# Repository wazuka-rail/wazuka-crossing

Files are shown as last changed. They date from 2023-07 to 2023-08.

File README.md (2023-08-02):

# Wazuka-Crossing
Miniature of a Japanese-style level crossing

## Full Version (with level crossing barriers)

**Under Development**

## Simple Version (without level crossing barriers)
Level Crossing Warning Sound Generator (https://www.youtube.com/watch?v=Fo-AsSxr2Go)

### Schematic
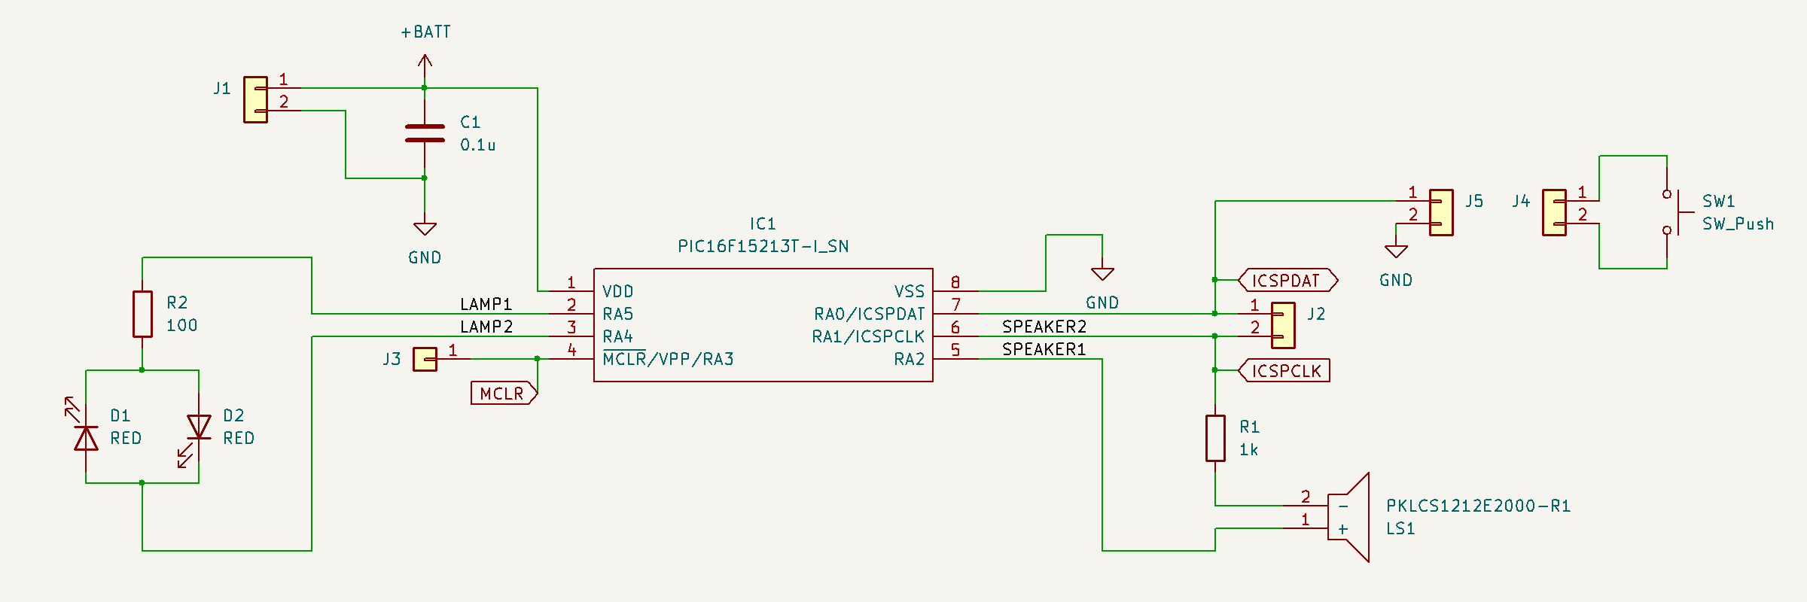
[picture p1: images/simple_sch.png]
Schematic of the simple version


### MCU
- PIC16F15213 PDIP / SOIC / DFN

|Pin| Name | Function | Target |
|---|---|---|---|
| 1 | VDD | VDD | |
| 2 | RA5 | DO | Lamp 1 |
| 3 | RA4 | DO | Lamp 2 |
| 4 | MCLR | MCLR | |
| 5 | PWM3 | PWM | Speaker 1 |
| 6 | ICSPCLK/PWM4 | ICSP/PWM | Speaker 2 |
| 7 | ICSPDAT | ICSP/DI  | Button |
| 8 | VSS | VSS | |

## Timers
| Freq.  | Timer | Purpose |
|---:|:---|---|
| 20 kHz | Timer2 | Sound PWM (PWM3) |
| 156 Hz | Timer2 / 128 | Lamp PFM (S/W) |
| ~30 Hz | Timer2 / 4 / ~150 | Sound Modulation |
| 20 Hz  | Timer0 | Train Detection, Button |
| 1.7 Hz | Timer0 / 12 | Lamp Flicker |

## Notes
The PICkit3 does not officially support the PIC16F152 family.
You can program PIC16F152 devices by PICkit3 with
[PICkitminus](http://kair.us/projects/pickitminus/).

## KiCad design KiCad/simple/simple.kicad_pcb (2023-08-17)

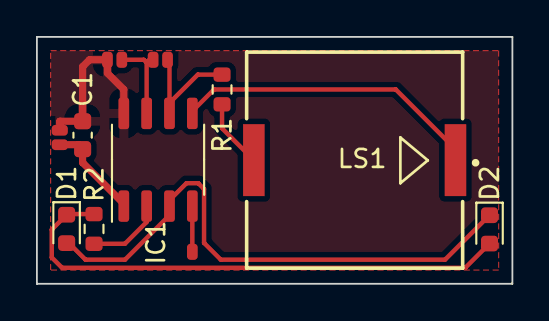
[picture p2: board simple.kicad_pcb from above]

Board: 2 copper layers, 26.4 x 13.7 mm, 11 parts (0 on the bottom side), 10 nets.

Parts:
C1: 0.1u; C_0603_1608Metric
D1, D2: RED; LED_0603_1608Metric
IC1: PIC16F15213T-I_SN; SO-8_3.9x4.9mm_P1.27mm
J1, J2, J5: Conn_01x02; JP_2T
J3: Conn_01x01; JP_1T
LS1: PKLCS1212E2000-R1
R1: 1k; R_0603_1608Metric
R2: 100; R_0603_1608Metric

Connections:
+BATT: C1.1, IC1.1 (VDD), J1.1
/LAMP1: IC1.2 (RA5), R2.1
/LAMP2: D1.2 (A), D2.1 (K), IC1.3 (RA4)
/SPEAKER1: IC1.5 (RA2), LS1.1 (+)
GND: C1.2, IC1.8 (VSS), J1.2, J5.2
ICSPCLK: IC1.6 (RA1/ICSPCLK), J2.2, R1.2
ICSPDAT: IC1.7 (RA0/ICSPDAT), J2.1, J5.1
MCLR: IC1.4 (~MCLR/VPP/RA3), J3.1
unnamed: D1.1 (K), D2.2 (A), R2.2
unnamed: LS1.2 (-), R1.1

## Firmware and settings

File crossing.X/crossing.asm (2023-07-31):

#ifdef  SIMPLE
    PROCESSOR 16F15213
#else
    PROCESSOR 16F15223
#endif

#include <xc.inc>

#include "macros.inc"

; CONFIG1
  CONFIG  FEXTOSC = OFF         ; External Oscillator Mode Selection bits (Oscillator not enabled)
  CONFIG  RSTOSC = HFINTOSC_32MHZ; Power-up Default Value for COSC bits (HFINTOSC (32 MHz))
  CONFIG  CLKOUTEN = OFF        ; Clock Out Enable bit (CLKOUT function is disabled; I/O function on RA4)
  CONFIG  VDDAR = LO            ; VDD Range Analog Calibration Selection bit (Internal analog systems are calibrated for operation between VDD = 1.8V - 3.6V)

; CONFIG2
  CONFIG  MCLRE = INTMCLR       ; Master Clear Enable bit (If LVP = 0, MCLR pin is port defined function; If LVP = 1, RA3 pin function is MCLR)
  CONFIG  PWRTS = PWRT_1        ; Power-up Timer Selection bits (PWRT set at 1 ms)
  CONFIG  WDTE = NSLEEP         ; WDT Operating Mode bits (WDT enabled while Sleep = 0, suspended when Sleep = 1; SEN is ignored)
  CONFIG  BOREN = NSLEEP        ; Brown-out Reset Enable bits (Brown-out Reset enabled while running, disabled in Sleep; SBOREN is ignored)
  CONFIG  BORV = LO             ; Brown-out Reset Voltage Selection bit (Brown-out Reset Voltage (VBOR) set to 1.9V)
  CONFIG  PPS1WAY = ON          ; PPSLOCKED One-Way Set Enable bit (The PPSLOCKED bit can be set once after an unlocking sequence is executed; once PPSLOCKED is set, all future changes to PPS registers are prevented)
  CONFIG  STVREN = ON           ; Stack Overflow/Underflow Reset Enable bit (Stack Overflow or Underflow will cause a reset)

; CONFIG3

; CONFIG4
  CONFIG  BBSIZE = BB512        ; Boot Block Size Selection bits (512 words boot block size)
  CONFIG  BBEN = OFF            ; Boot Block Enable bit (Boot Block is disabled)
  CONFIG  SAFEN = OFF           ; SAF Enable bit (SAF is disabled)
  CONFIG  WRTAPP = OFF          ; Application Block Write Protection bit (Application Block is not write-protected)
  CONFIG  WRTB = OFF            ; Boot Block Write Protection bit (Boot Block is not write-protected)
  CONFIG  WRTC = OFF            ; Configuration Registers Write Protection bit (Configuration Registers are not write-protected)
  CONFIG  WRTSAF = OFF          ; Storage Area Flash (SAF) Write Protection bit (SAF is not write-protected)
  CONFIG  LVP = ON              ; Low Voltage Programming Enable bit (Low Voltage programming enabled. MCLR/Vpp pin function is MCLR. MCLRE Configuration bit is ignored.)

; CONFIG5
  CONFIG  CP = OFF              ; User Program Flash Memory Code Protection bit (User Program Flash Memory code protection is disabled)


; Common    0x70-0x7F 16 bytes
;-------------------------------------------------------------------------------
ALERT_STATE     equ 0x70
#define STATE_R     ALERT_STATE, 0
#define STATE_A     ALERT_STATE, 1
#define STATE_B     ALERT_STATE, 2
#define STATE_C     ALERT_STATE, 3
#define STATE_D     ALERT_STATE, 4


TIMER           equ 0x71
#define TIMER_20HZ  TIMER, 0

; Button Count
BUTTON_DOWN_COUNT   equ 0x74
BUTTON_UP_COUNT     equ 0x75
BUTTON_STATE        equ 0x76
#define BUTTON_CLICKED  BUTTON_STATE, 0
#define BUTTON_CLICKED1 BUTTON_STATE, 1
#define BUTTON_CLICKED2 BUTTON_STATE, 2
#define BUTTON_CLICKED3 BUTTON_STATE, 3
#define BUTTON_CLICKED4 BUTTON_STATE, 4
#define BUTTON_CLICKED5 BUTTON_STATE, 5
#define BUTTON_CLICKED6 BUTTON_STATE, 6


; BANK 0    0x20-0x6F 80 bytes
;-------------------------------------------------------------------------------

; Lamp Flicker
FLICKER_COUNT   equ 0x24
FLICKER_STATE   equ 0x25
; Lamp PWM
LAMP_PFM_COUNT  equ 0x26
LAMP_PFM_CYCLE  equ 0x27


; Sound Oscillator 1
OSC1_ACC_L      equ 0x30
OSC1_ACC_H      equ 0x31
OSC1_DELTA      equ 0x32
OSC1_AMP        equ 0x33
OSC1_ATT        equ 0x34

; Sound Oscillator 2
OSC2_ACC_L      equ 0x35
OSC2_ACC_H      equ 0x36
OSC2_DELTA      equ 0x37
OSC2_AMP        equ 0x38    ; not used
OSC2_ATT        equ 0x39

; WaveTableSelector
WAVE_TABLE_L    equ 0x3A
WAVE_TABLE_H    equ 0x3B

; Envelope Modulator
ENVELOPE_COUNT_L equ 0x3C
ENVELOPE_COUNT_H equ 0x3D
ENVELOPE_CYCLE   equ 0x3E

;-------------------------------------------------------------------------------
; Pin
#ifdef  SIMPLE

BUTTON      equ 0 ; RA0
LAMP1       equ 5 ; RA5
LAMP2       equ 4 ; RA4
SPEAKER1    equ 1 ; RA1
SPEAKER2    equ 2 ; RA2

#else

BUTTON      equ 1 ; RA1
LAMP1       equ 5 ; RA5
LAMP2       equ 4 ; RA4
SPEAKER     equ 5 ; RC5
#endif

;-------------------------------------------------------------------------------
    PSECT resetVec, abs, class=CODE, delta=2
    ORG         0
    goto        Initialize
;-------------------------------------------------------------------------------
    PSECT intVec, abs, class=CODE, delta=2
    ORG         4
Interrupt:
    banksel     PIR1
InterruptTimer2:
    btfss       TMR2IF
    goto        InterruptTimer1

    ; 20 kHz
    bcf         TMR2IF

#ifndef SIMPLE
    goto        SetSoundPWM
SetMotorPDM:

#endif
SetSoundPWM:
    btfsc       STATE_R
    retfie

    banksel     LATA
    movfw       WAVE_TABLE_H
    movwf       FSR0H

    movfw       OSC1_DELTA
    addwf       OSC1_ACC_L, F
    skpnc
    incf        OSC1_ACC_H, F
    movfw       OSC1_ACC_H
    andlw       0x0F
    addwf       WAVE_TABLE_L, W
    addwf       OSC1_ATT, W
    skpnc
    iorlw       0xF0    ; clamp
    movwf       FSR0L   ; FSR0L = min(WAVE_TABLE_L + OSC1_ATT) + phase
    movfw       INDF0
    movwf       OSC1_AMP

    movfw       OSC2_DELTA
    addwf       OSC2_ACC_L, F
    skpnc
    incf        OSC2_ACC_H, F
    movfw       OSC2_ACC_H
    andlw       0x0F
    addwf       WAVE_TABLE_L, W
    addwf       OSC2_ATT, W
    skpnc
    iorlw       0xF0    ; clamp
    movwf       FSR0L   ; FSR0L = min(WAVE_TABLE_L + OSC2_ATT) + phase
    movfw       INDF0   ; W = OSC2_AMP

    addwf       OSC1_AMP, W ; W = OSC1_AMP + OSC2_AMP
    rrf         WREG, F     ; W = (OSC1_AMP + OSC2_AMP) >> 1
    banksel     PWM3DCH
    movwf       PWM3DCH
#ifdef  SIMPLE
    movwf       PWM4DCH
#endif
    clrf        PWM3DCL
    rrf         PWM3DCL, F  ; bit7: (OSC1_AMP + OSC2_AMP) & 1
#ifdef  SIMPLE
    movfw       PWM3DCL
    movwf       PWM4DCL
#endif

ProcLampPFM:
    banksel     LATA
    movlw       (1 << LAMP1) | (1 << LAMP2) ; off
    decf        LAMP_PFM_COUNT, F
    skpz
    goto        ProcLampPFMOff
    movfw       LAMP_PFM_CYCLE
    movwf       LAMP_PFM_COUNT
    movfw       FLICKER_STATE ; on or default
ProcLampPFMOff:
    movwf       LATA

ProcSoundEnvelope:
    decfsz      ENVELOPE_COUNT_L, F
    retfie
    ; ~ 130 Hz
    movfw       ENVELOPE_CYCLE
    movwf       ENVELOPE_COUNT_L

    decfsz      ENVELOPE_COUNT_H, F
    retfie
    ; ~ 32 Hz
    movlw       4          ; 20 kHz / CYCLE / 4 = 5 kHz / CYCLE
    movwf       ENVELOPE_COUNT_H

    movlw       0x10
    addwf       WAVE_TABLE_L, F    ; change envelope
    retfie
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

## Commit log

2023-08-02 Add the KiCad project for the simple version
    [simple.kicad_pcb, simple.kicad_sch]
2023-08-02 Add the schematic image to README.md
2023-08-04 Add the title data of PCB
    [simple.kicad_pcb]
2023-08-17 Fix the footprint of C1
    [simple.kicad_pcb, simple.kicad_sch]
